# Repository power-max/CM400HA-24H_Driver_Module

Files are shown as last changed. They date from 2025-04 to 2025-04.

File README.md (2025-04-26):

# CM400HA-24H driver
Simple IGBT driver module for Mitubisi IGBT CM400HA-24H modules. This driver module should be capable of switching at up to 100kHz, limited by the SN6505 based DC-DC isolation converter.

The 7741F digital isolator IC is chosen for good CMTI, low propagation delay, high speed, low cost, and the 3 useful return digital channels. 2 standard DIP8 low side driver ICs are used for driving the gate, with 16/20A current capability with the outputs paralelled. In the future I may modify the footprint to allow the use of cheaper SO8 SMD alternative parts as well, or opt for inverting gate drivers and the 7741 (default HIGH state, active low) IC. 

The board features 2 collector voltage feedbacks, one intended for desaturation detection and one for VCC/2 crossover detection to allow output bridge voltage sensing. exact resistor values will need to be determined by the system integrator. There is also feedback for UV lockout with the Pgood return signal. Note: at present there is no fault shutdown, as the active HIGH input to the module directly controls the gate of the IGBT. All shutdown protections should be implemented on an upstream controller.

THE DESIGN IS PROVIDED “AS IS”, WITHOUT WARRANTY OF ANY KIND, EXPRESS OR IMPLIED, INCLUDING BUT NOT LIMITED TO THE WARRANTIES OF MERCHANTABILITY, FITNESS FOR A PARTICULAR PURPOSE AND NONINFRINGEMENT. Refer to the TAPR hardware license for additional detail.

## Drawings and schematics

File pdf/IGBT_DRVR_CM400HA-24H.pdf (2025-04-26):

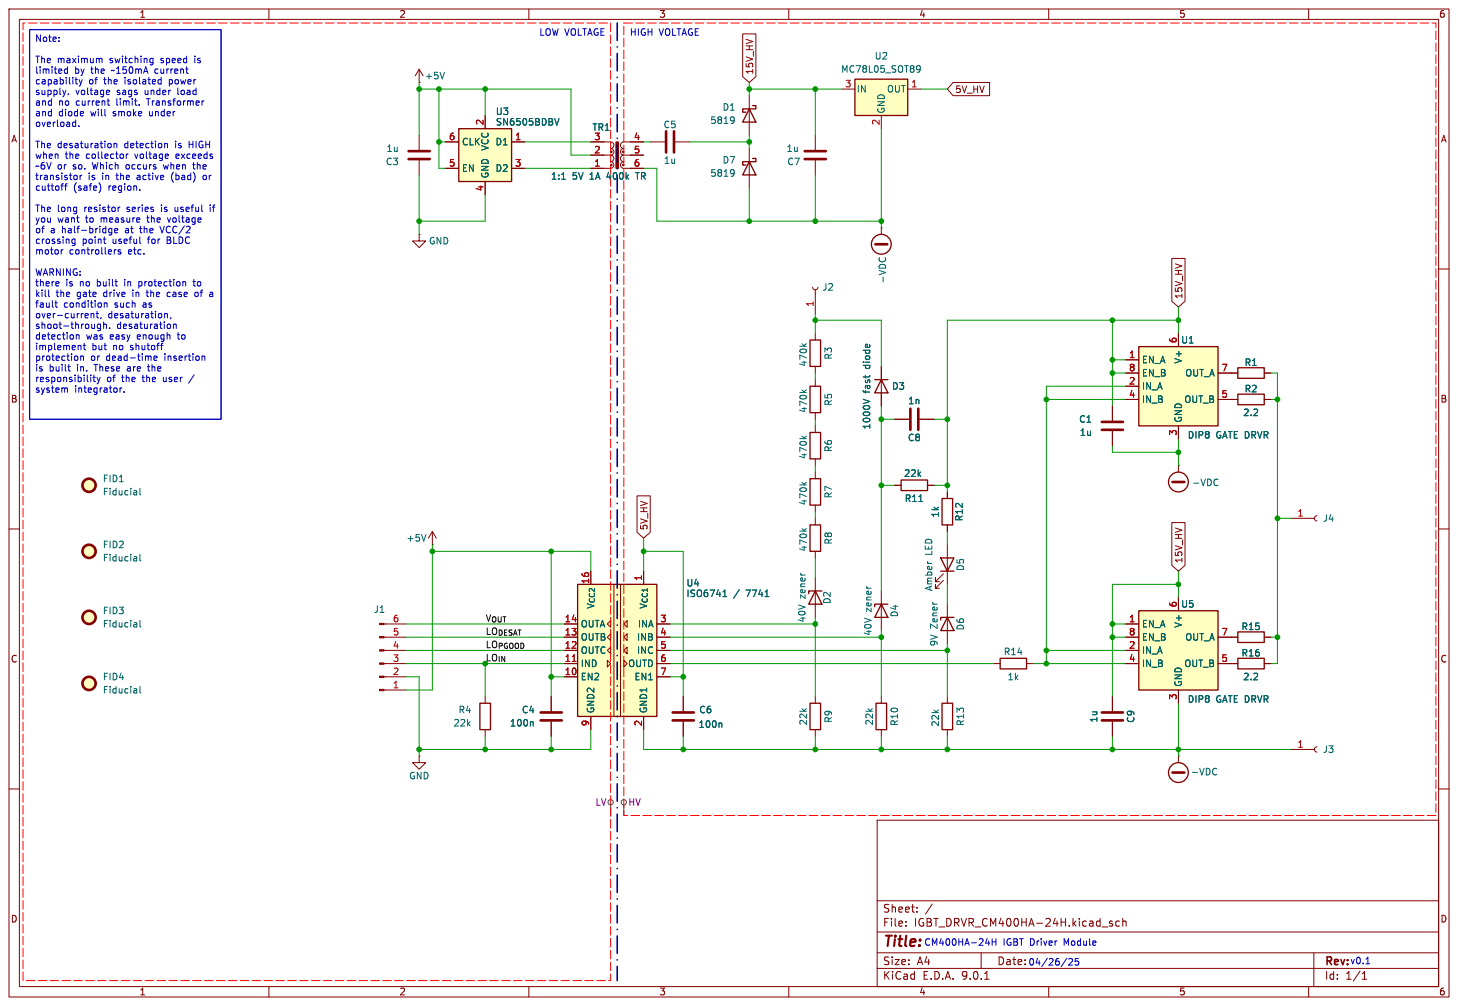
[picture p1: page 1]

kill the gate drive in the case of a

is built in. These are the

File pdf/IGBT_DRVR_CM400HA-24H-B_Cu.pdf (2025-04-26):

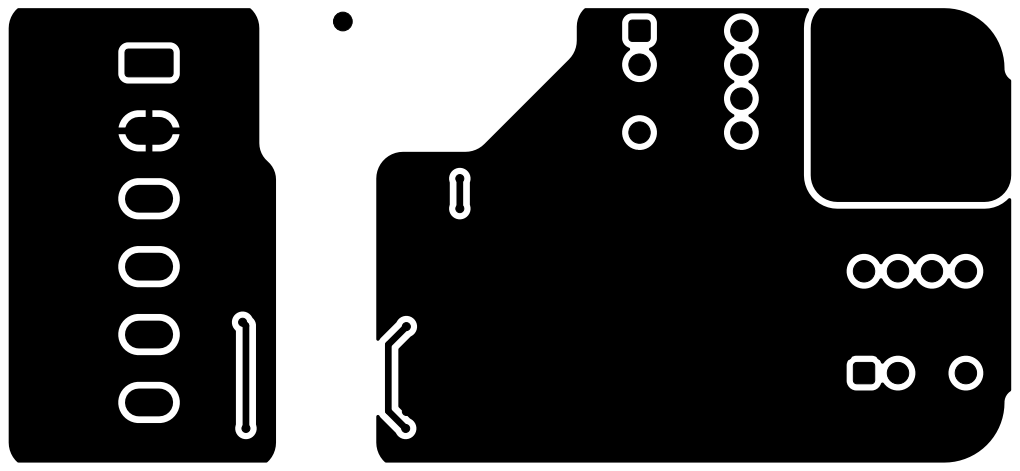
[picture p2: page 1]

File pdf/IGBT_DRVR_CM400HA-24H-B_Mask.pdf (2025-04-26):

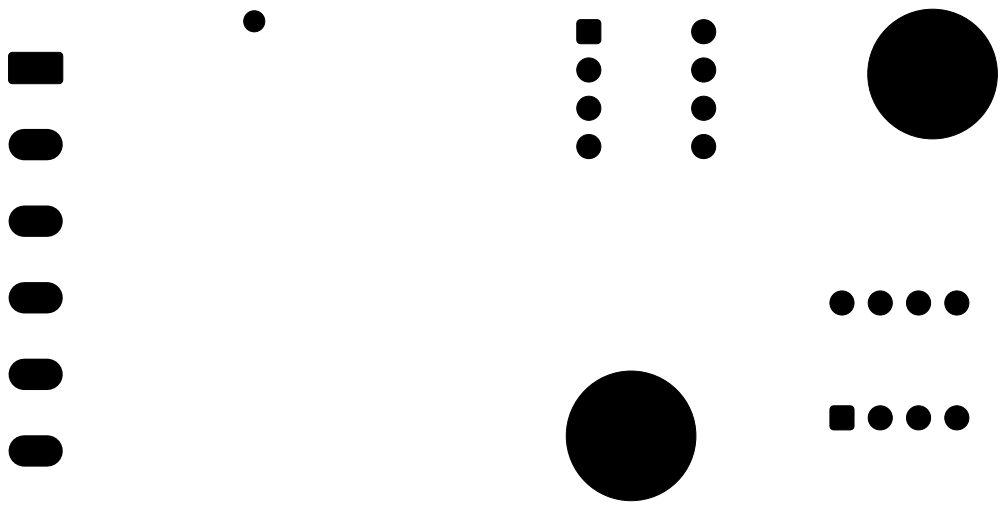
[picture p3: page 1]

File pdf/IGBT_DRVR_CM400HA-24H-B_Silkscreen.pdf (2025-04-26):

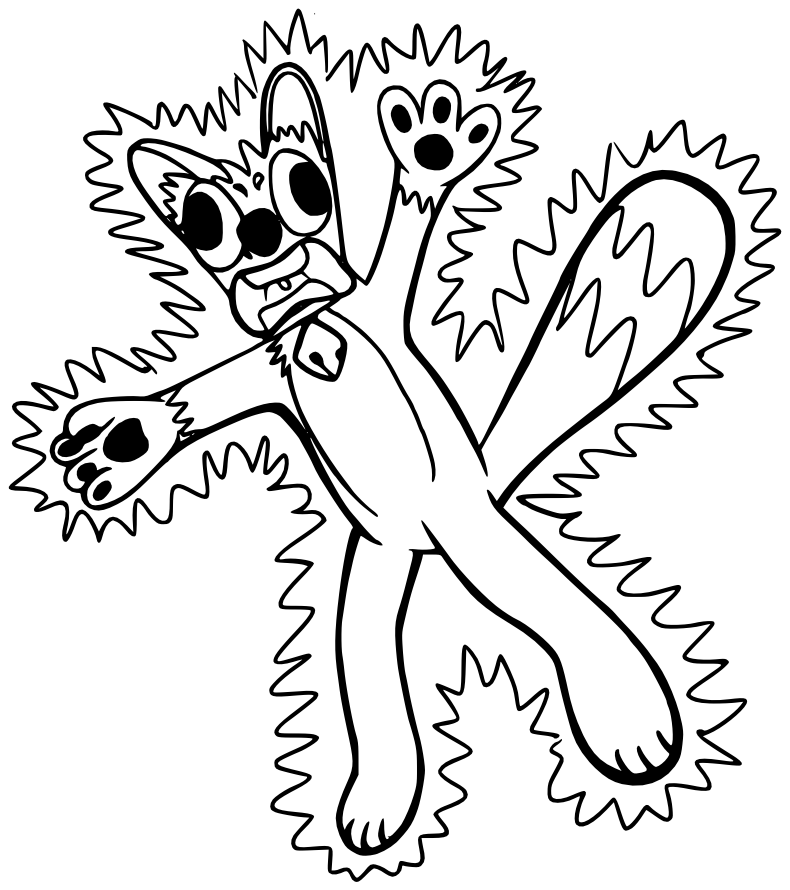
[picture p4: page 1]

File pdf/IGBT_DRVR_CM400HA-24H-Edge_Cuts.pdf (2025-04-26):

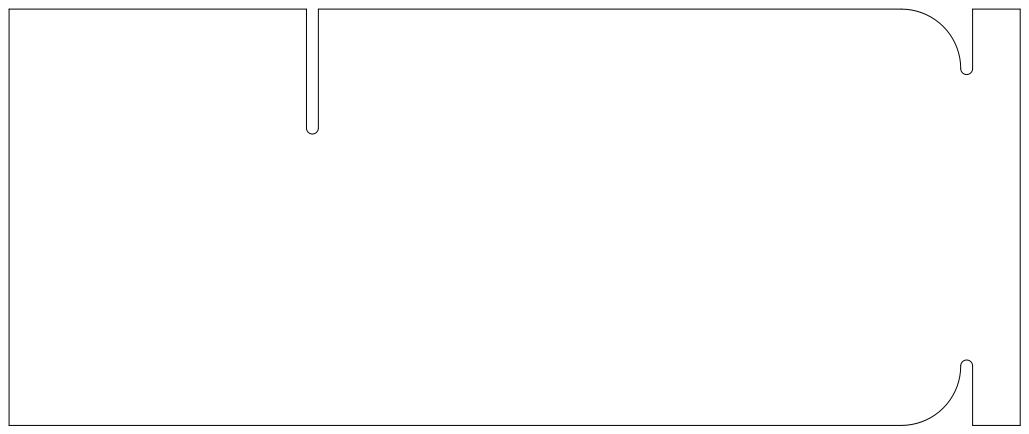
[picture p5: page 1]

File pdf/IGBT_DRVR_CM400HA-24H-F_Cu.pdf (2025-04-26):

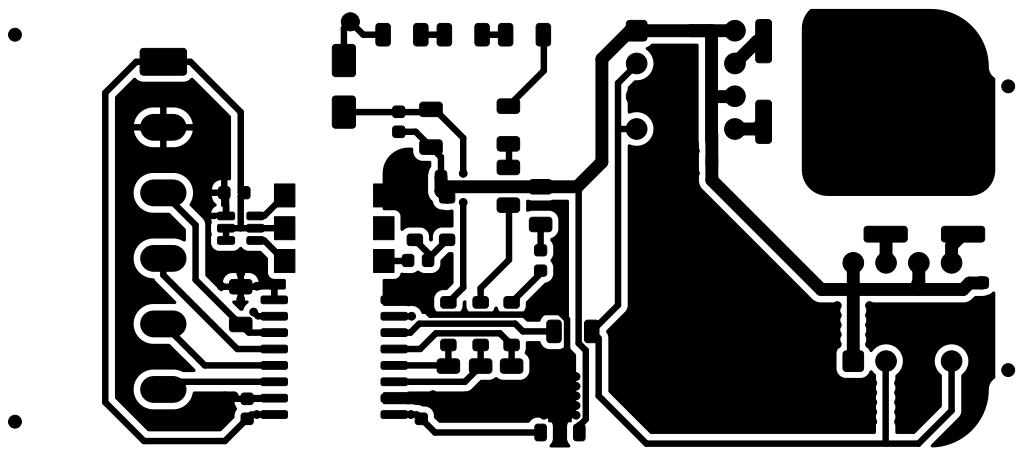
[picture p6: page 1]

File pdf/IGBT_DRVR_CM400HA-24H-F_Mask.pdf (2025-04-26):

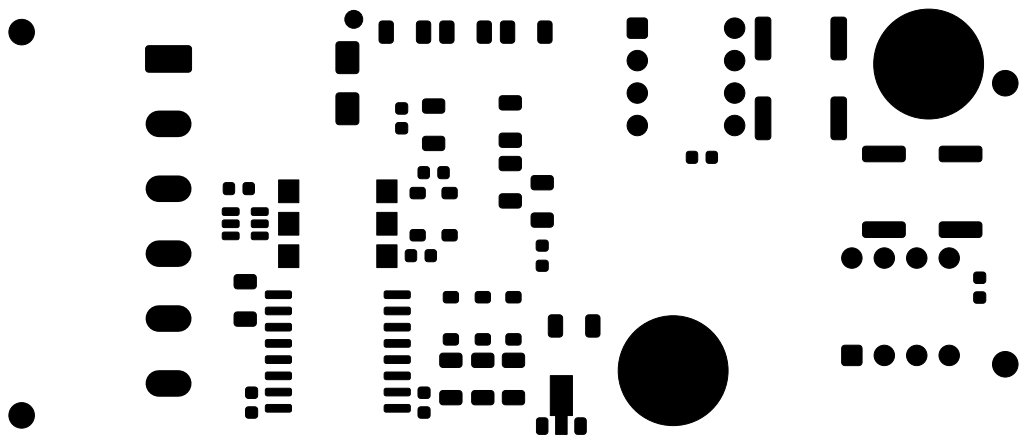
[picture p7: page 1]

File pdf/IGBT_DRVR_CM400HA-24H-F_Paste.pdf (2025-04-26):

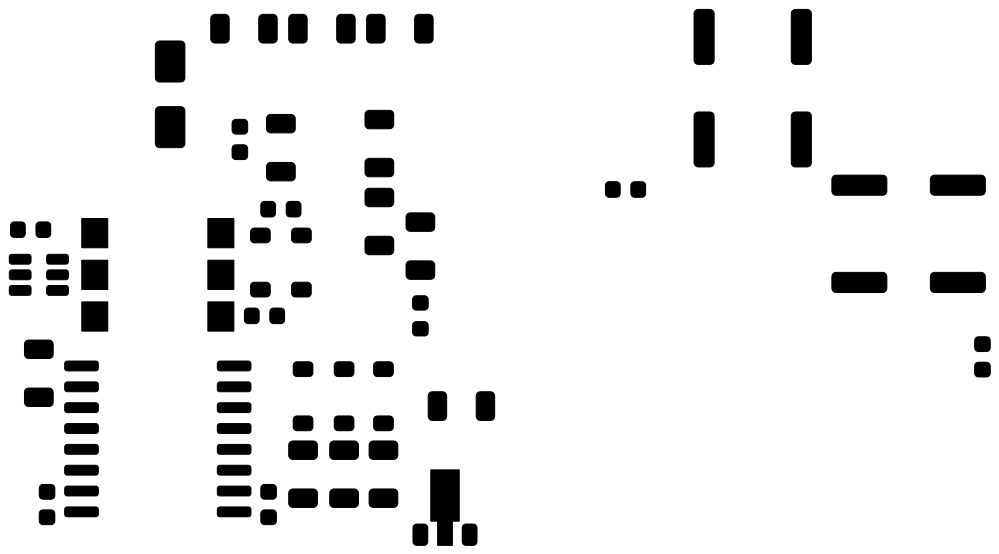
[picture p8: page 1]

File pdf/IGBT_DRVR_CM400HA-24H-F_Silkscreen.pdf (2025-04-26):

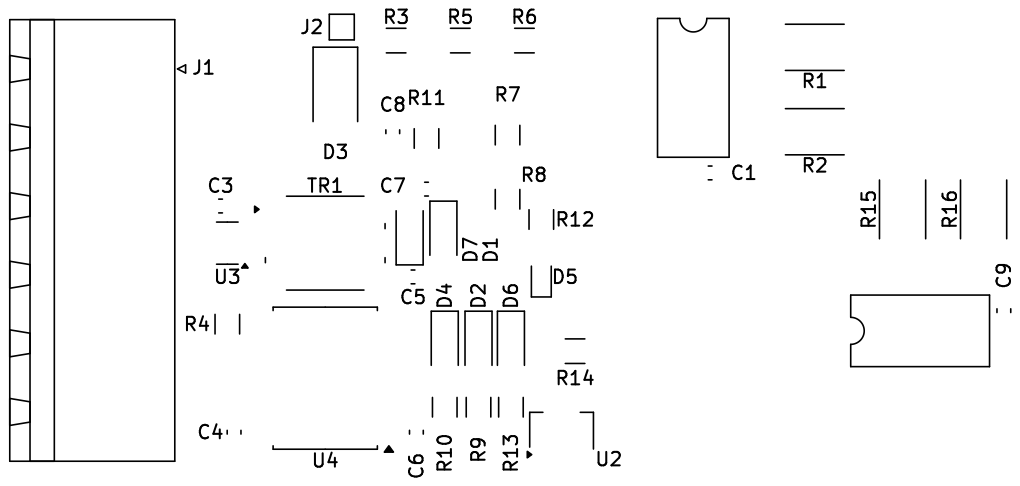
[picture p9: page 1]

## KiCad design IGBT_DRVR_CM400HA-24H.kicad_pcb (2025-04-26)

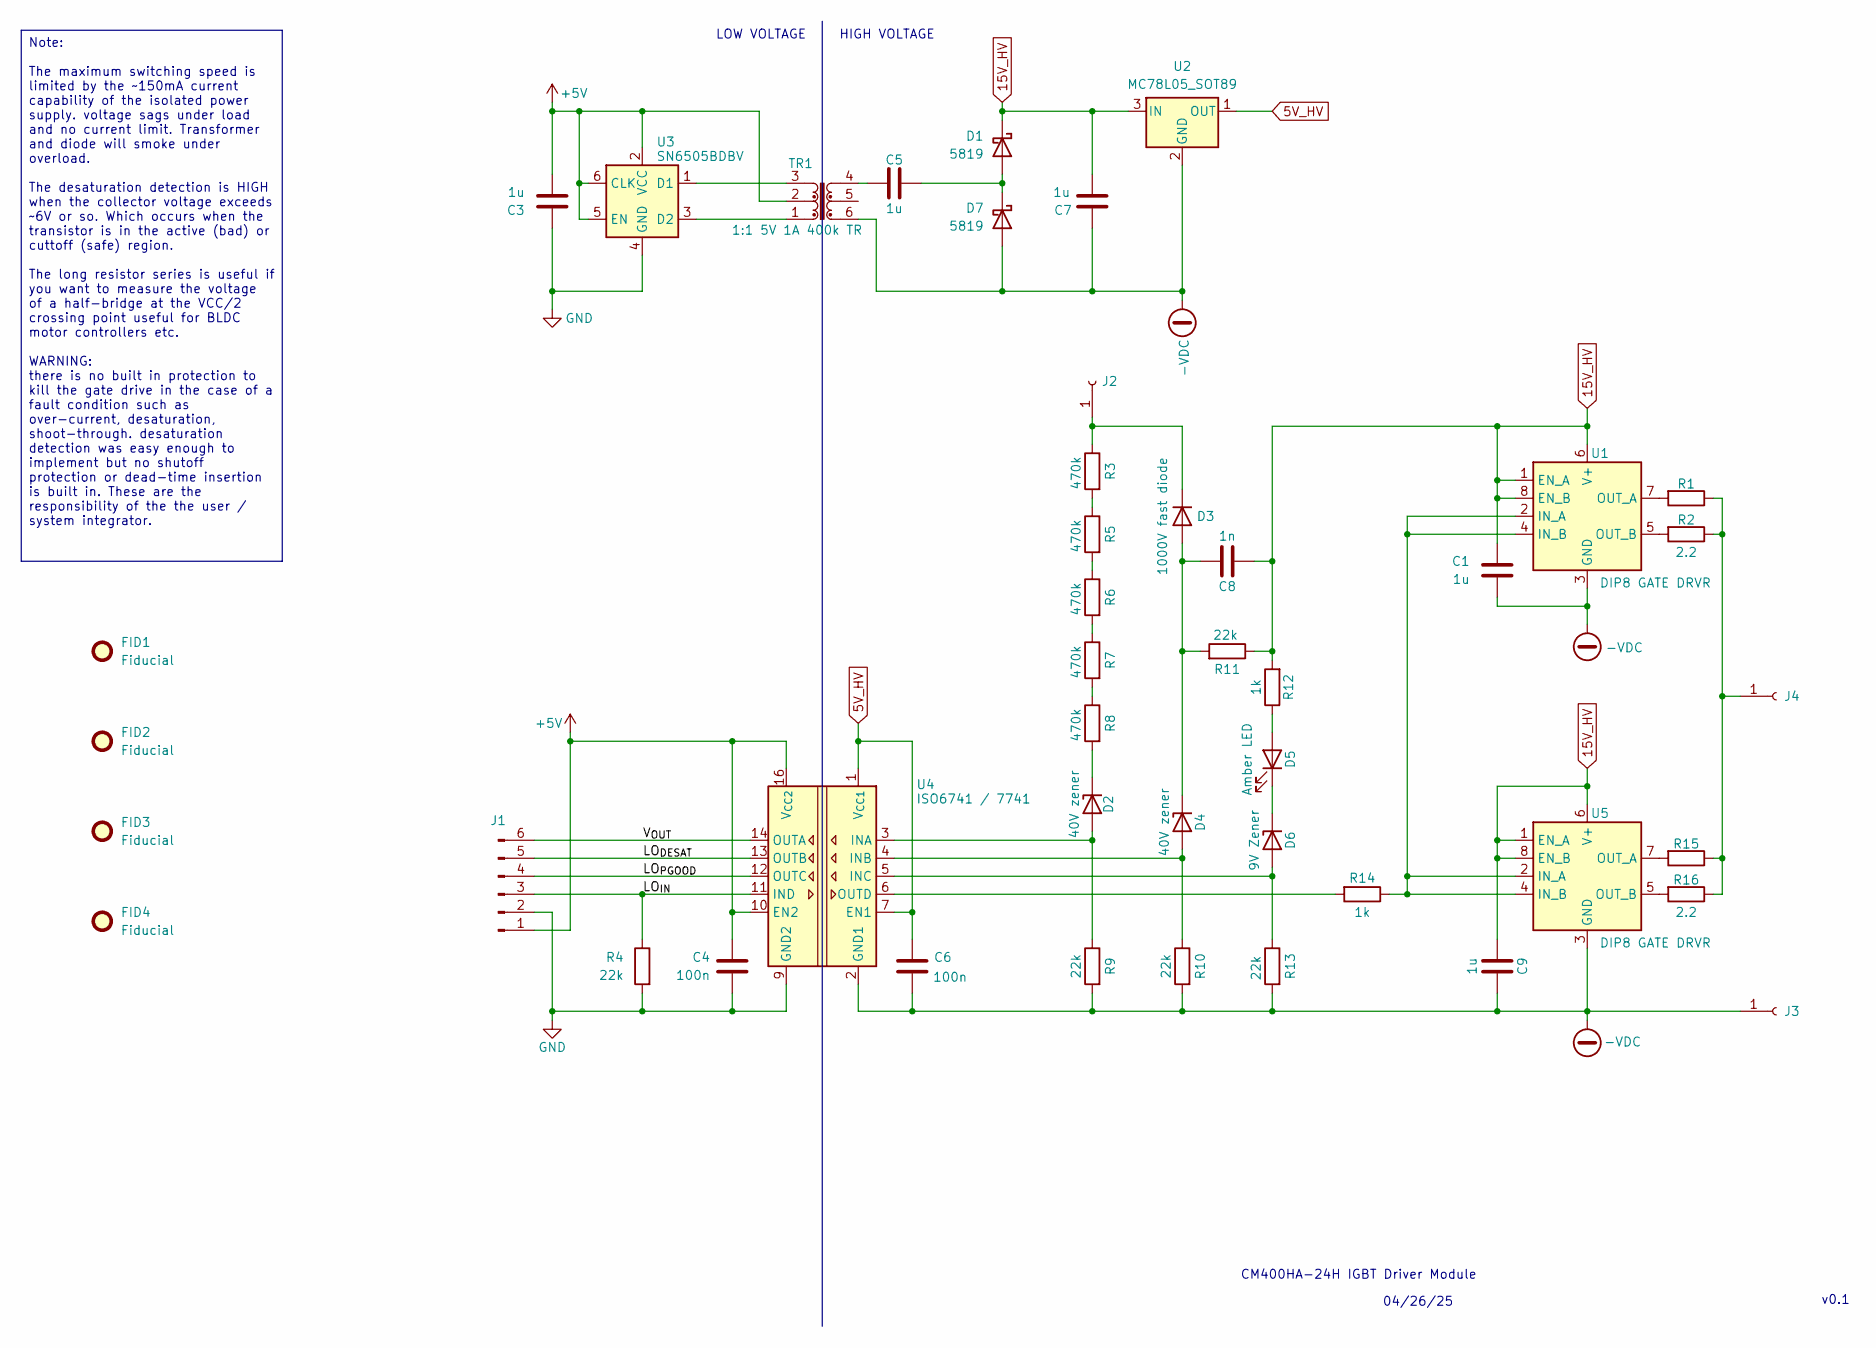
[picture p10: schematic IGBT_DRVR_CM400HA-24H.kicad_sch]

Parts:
C1, C3, C5, C7, C9: 1u; C_0603_1608Metric
C4, C6: 100n; C_0603_1608Metric
C8: 1n; C_0603_1608Metric
D1, D7: 5819; D_SOD-123; LCSC C8598
D2, D4: 40V zener; D_SOD-123; LCSC C550214
D3: 1000V fast diode; D_SMA; LCSC C18199160
D5: Amber LED; LED_0603_1608Metric; LCSC C7496818
D6: 9V Zener; D_SOD-123; LCSC C19077407
FID1, FID2, FID3, FID4: Fiducial; Fiducial_1mm_Mask2mm
J1: MSTBA 5.08 terminal block; PhoenixContact_MSTBA_2,5_6-G-5,08_1x06_P5.08mm_Horizontal; LCSC C42378073
J2: direct wire with lug; Pin_D0.7mm_L6.5mm_W1.8mm_FlatFork
J3, J4: hole; MountingHole_4.3mm_M4_Pad_Via
R1, R2, R15, R16: 2.2; R_2512_6332Metric
R3, R5, R6, R7, R8: 470k; R_1206_3216Metric
R4, R9, R10, R11, R13: 22k; R_1206_3216Metric
R12, R14: 1k; R_1206_3216Metric
TR1: 1:1 5V 1A 400k TR; Pulse_PA2004NL; LCSC C42422416
U1, U5: DIP8 GATE DRVR; DIP-8_W7.62mm; LCSC C2874007
U2: MC78L05_SOT89; SOT-89-3; LCSC C42738
U3: SN6505BDBV; SOT-23-6; LCSC C2156022
U4: ISO6741 / 7741; SOIC-16W_7.5x10.3mm_P1.27mm; LCSC C2872241

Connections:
5V_HV: C6.1, U2.1 (OUT), U4.1 (V_{CC1}), U4.7 (EN1)
15V_HV: C1.1, C7.2, C8.1, C9.1, D1.1 (K), R11.1, R12.2, U1.1 (EN_A), U1.6 (V+), U1.8 (EN_B), U2.3 (IN), U5.1 (EN_A), U5.6 (V+), U5.8 (EN_B)
+5V: C3.2, C4.1, J1.1, TR1.2, U3.2 (VCC), U3.5 (EN), U3.6 (CLK), U4.10 (EN2), U4.16 (V_{CC2})
-VDC: C1.2, C6.2, C7.1, C9.2, D7.2 (A), J3.1, R9.2, R10.2, R13.2, TR1.6, U1.3 (GND), U2.2 (GND), U4.2 (GND1), U4.8 (GND1), U5.3 (GND)
/LO_{DESAT}: J1.5, U4.13 (OUTB)
/LO_{IN}: J1.3, R4.1, U4.11 (IND)
/LO_{PGOOD}: J1.4, U4.12 (OUTC)
/V_{OUT}: J1.6, U4.14 (OUTA)
GND: C3.1, C4.2, J1.2, R4.2, U3.4 (GND), U4.9 (GND2), U4.15 (GND2)
unnamed: C5.1, TR1.4
unnamed: C5.2, D1.2 (A), D7.1 (K)
unnamed: D2.2 (A), R9.1, U4.3 (INA)
unnamed: D2.1 (K), R8.2
unnamed: C8.2, D3.2 (A), D4.1 (K), R11.2
unnamed: D3.1 (K), J2.1, R3.1
unnamed: D4.2 (A), R10.1, U4.4 (INB)
unnamed: D5.2 (A), R12.1
unnamed: D5.1 (K), D6.1 (K)
unnamed: D6.2 (A), R13.1, U4.5 (INC)
unnamed: J4.1, R1.1, R2.1, R15.1, R16.1
unnamed: R3.2, R5.1
unnamed: R5.2, R6.1
unnamed: R6.2, R7.1
unnamed: R7.2, R8.1
unnamed: R14.1, U1.2 (IN_A), U1.4 (IN_B), U5.2 (IN_A), U5.4 (IN_B)
unnamed: R1.2, U1.7 (OUT_A)
unnamed: R2.2, U1.5 (OUT_B)
unnamed: TR1.3, U3.1 (D1)
unnamed: TR1.1, U3.3 (D2)
unnamed: R14.2, U4.6 (OUTD)
unnamed: R15.2, U5.7 (OUT_A)
unnamed: R16.2, U5.5 (OUT_B)

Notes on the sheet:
HIGH VOLTAGE
LOW VOLTAGE
CM400HA-24H IGBT Driver Module
04/26/25
v0.1
Note: The maximum switching speed is limited by the ~150mA current capability of the isolated power supply. voltage sags under load and no current limit. Transformer and diode will smoke under overload. The desaturation detection is HIGH when the collector voltage exceeds ~6V or so. Which occurs wh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

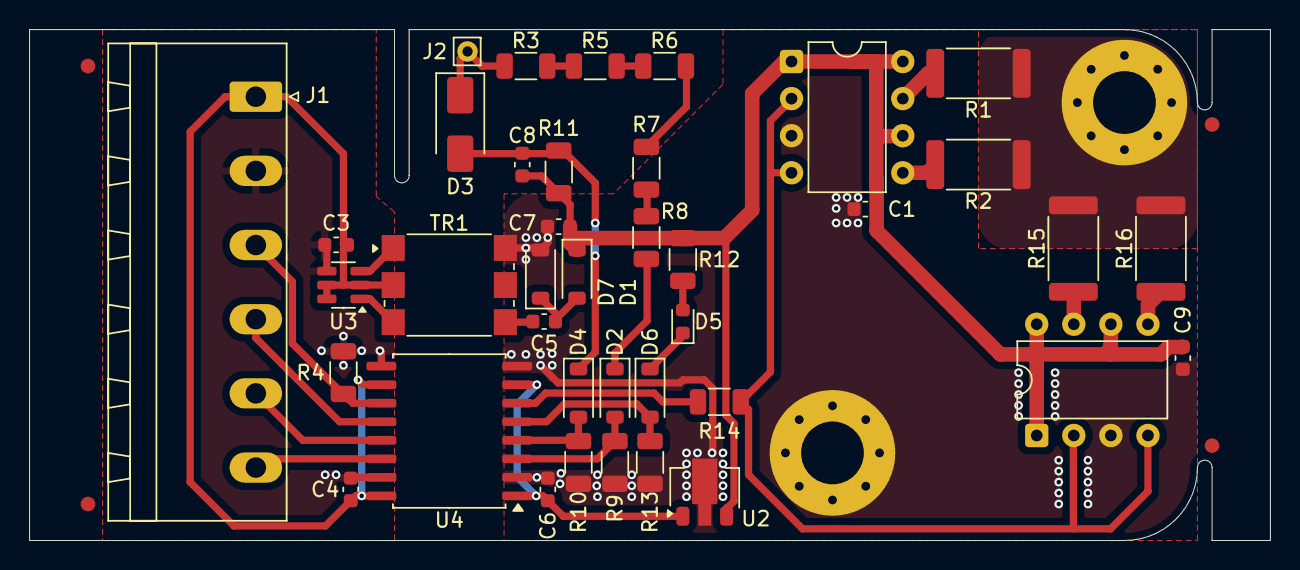
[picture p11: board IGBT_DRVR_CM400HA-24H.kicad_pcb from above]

Board: 2 copper layers, 85.0 x 35.0 mm, 45 parts (0 on the bottom side), 32 nets.

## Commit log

2025-04-26 initial commit of v0.1
    [IGBT_DRVR_CM400HA-24H-B_Cu.gbr, IGBT_DRVR_CM400HA-24H-B_Mask.gbr, IGBT_DRVR_CM400HA-24H-B_Paste.gbr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]
2025-04-26 decided to remove the PCBA files from github as they are generated from the source files and would need to be generated by the user in accordance to their chosen fab house.
    [IGBT_DRVR_CM400HA-24H-B_Cu.gbr, IGBT_DRVR_CM400HA-24H-B_Mask.gbr, IGBT_DRVR_CM400HA-24H-B_Paste.gbr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]
2025-04-26 removed reference to now defunct PCBA folder
